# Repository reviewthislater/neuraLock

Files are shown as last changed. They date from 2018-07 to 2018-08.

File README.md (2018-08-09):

<div align="center">

# neuraLock



#### A proof of concept safe utilizing deep learning for facial, vocal, and word recognition.
#### Contains code and STLS to build your own nueraLock safe

 []()

</div>

## Hardware
[Raspberry Pi 3 Model B](https://www.amazon.com/gp/product/B01LPLPBS8/ref=oh_aui_detailpage_o00_s00?ie=UTF8&psc=1): $35.99

[Samsung Evo Micro SD](https://www.amazon.com/Samsung-MicroSDXC-Adapter-MB-ME64GA-AM/dp/B06XX29S9Q): $17.99

[Keyboard w/ trackpad](https://www.amazon.com/Rii-Wireless-Keyboard-Touchpad-Control/dp/B00I5SW8MC): $15.95

[Traxxas Servo](https://www.amazon.com/dp/B000XQ3G3E): $26.05

[ELP Mini USB Camera](https://www.amazon.com/gp/product/B01DRJXDEA): $29.99

[Lavalier Mini USB Microphone](https://www.amazon.com/gp/product/B074BLM973): $14.99

[5000 mAh External Battery](https://www.amazon.com/gp/product/B00MWU1GGI): $11.99

[Assorted LEDS](https://www.amazon.com/Lights-Emitting-Assortment-Arduino-300-Pack/dp/B00UWBJM0Q): $9.99

[Tactile Switches](https://www.amazon.com/Uxcell-a15111200ux1613-Momentary-Tactile-Terminal/dp/B019DCWTSQ): $7.46

3d printer and filament: $??.??

#### Total Cost: 170.40 + ??.??

All of these parts except for the raspberry pi 3 can be exchanged with similar parts, the provided links provide either the exact or similar hardware I used.

## Setup & Install
### Clone the repository
```bash
cd ~
git clone https://github.com/alexanderepstein/neuraLock
```
### Enter the repository
```bash
cd neuraLock
```
### Run environment build script
```
./env.sh
```
The script will ask for sudo privileges.
### Build training dataset
For both image and audio data the folder structure should look like
```bash
├── AudioData
│   ├── Subject1
│   │   ├── file1.wav
│   │   ├── file2.wav
│   │   ├── file3.wav
│   ├── Subject2
│   │   ├── file1.wav
│   │   ├── file2.wav
│   ├── Subject3
│   │   ├── file1.wav
│   │   ├── file2.wav
│   │   ├── file3.wav
```

### Gathering Face Training Data
I used about 8 subjects from the [Yale Faces Extended B](http://vision.ucsd.edu/~leekc/ExtYaleDatabase/ExtYaleB.html) training set, the larger the number of subjects used the more robust the classifier will be. Also make sure to include pictures of any users you would like to be able to be validated for entering the safe, for better results take pictures with the same camera that will be used for prediction.

### Gathering Audio Training Data
I used about 5 subjects from the [VoxForge dataset](http://www.repository.voxforge1.org/downloads/SpeechCorpus/Trunk/Audio/Original/), it is useful to utilize training data with the same sampling rate as your microphone. It is also useful to get training data from the same individual recorded at different times, something like [Angus-CJG](http://www.repository.voxforge1.org/downloads/SpeechCorpus/Trunk/Audio/Original/48kHz_16bit/Angus-20080320-cjg.tgz)
and [Angus-NDD](http://www.repository.voxforge1.org/downloads/SpeechCorpus/Trunk/Audio/Original/48kHz_16bit/Angus-20080320-ndd.tgz) the wav files from both of these archives would go under one folder named Angus in the AudioData root directory. It is helpful to also record empty noise with about 10-20 samples 5 seconds each. This will classify noise with no speaker as this dummy subject. Finally make sure to record audio of any user you would like to be able to be validated for entering the safe, for better results record the audio with the same microphone that will be used for prediction.

### Wiring The Hardware
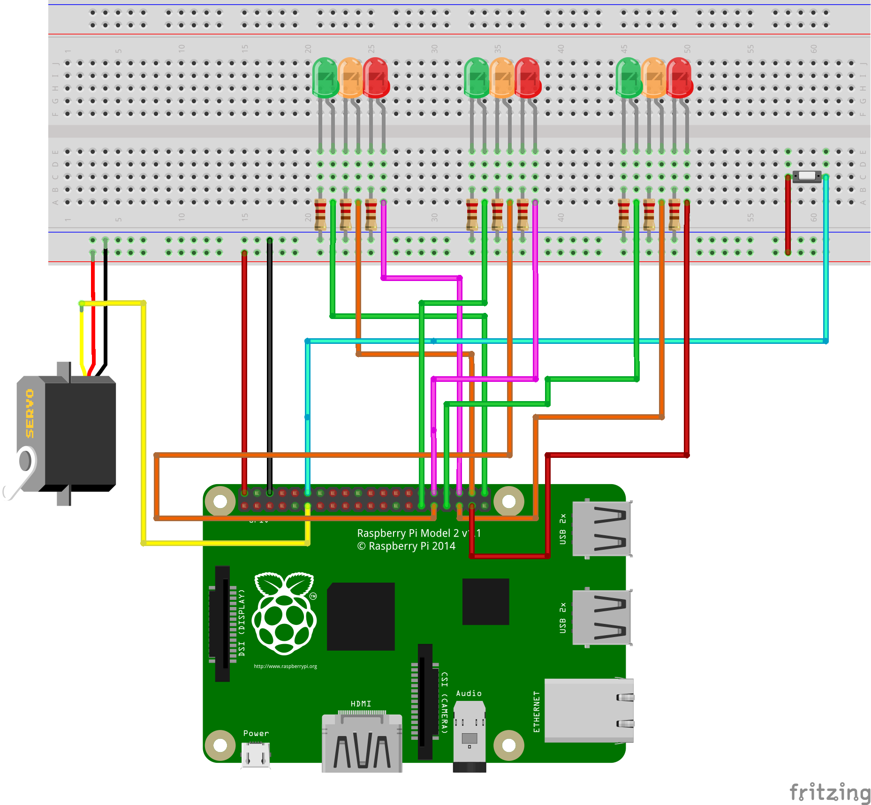
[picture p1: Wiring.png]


The pin layout will be treated as BCM, to see what that looks like visit [here](https://gpiozero.readthedocs.io/en/stable/recipes.html#pin-numbering)

| Component | GPIO |
|:---:|---|
| Servo |  17  |
| Push Button |  18  |
| Safe Green LED |  21  |
| Safe Orange LED  |  20  |
| Safe Red LED |  16  |
| Face Green LED |  13  |
| Face Orange LED  |  19  |
| Face Red LED |  26  |
| Voice Green LED  | 5  |
| Voice Orange LED | 6  |
| Voice Red LED |  12  |

### Executing the program

#### Command line arguments
```bash
-ad AUDIO_DATASET, --audio_dataset AUDIO_DATASET
                      path to audio training data
 -fd FACE_DATASET, --face_dataset FACE_DATASET
                       path to face training data
 -vm VOICE_MODEL, --voice_model VOICE_MODEL
                       path to serialized voice model
 -fm FACE_MODEL, --face_model FACE_MODEL
                       path to serialized face model
 -lv, --load_voice_model
                       boolean for loading voice model
 -lf, --load_face_model
                       boolean for loading face model
 -u UNLOCK_PHRASE, --unlock_phrase UNLOCK_PHRASE
                       unlock phrase
 -am {both,face,voice}, --authentication_model {both,face,voice}
                       choose the authentication model
 -vu VALID_USERS [VALID_USERS ...], --valid_users VALID_USERS [VALID_USERS ...]
                       users the safe should open for
```
A valid execution of the program might look like
```bash
./controller.py -ad "AudioData" -fd "ImageData" -vm "voiceModel.bin" -fm "imageEncodings.bin" -lv -am both -vu Alex
# Execute the program, audio data is located in AudioData, image data is contained in "ImageData", the voice model should be read to/written from "voiceModel.bin", the face encodings should be read to/written from "imageEncodings.bin", load the voice model, authenticate using both voice and face, set Alex as a valid user
```

### Current State
The STLS are not perfectly designed for the hardware, not enough testing was able to be done before confirm the design. However you can (force) the design to work by drilling and hot glue. You can use the STL's as a reference or starting point for what the safe will look like. Hopefully we will have time in the future to perfect the design.

### Issues
For any issues please open a new issue in the issue tracker [here](https://github.com/alexanderepstein/neuraLock/issues/new)

## License

MIT License

Copyright (c) 2018 Alex Epstein

Permission is hereby granted, free of charge, to any person obtaining a copy of this software and associated documentation files (the "Software"), to deal in the Software without restriction, including without limitation the rights to use, copy, modify, merge, publish, distribute, sublicense, and/or sell copies of the Software, and to permit persons to whom the Software is furnished to do so, subject to the following conditions:

The above copyright notice and this permission notice shall be included in all copies or substantial portions of the Software.

THE SOFTWARE IS PROVIDED "AS IS", WITHOUT WARRANTY OF ANY KIND, EXPRESS OR IMPLIED, INCLUDING BUT NOT LIMITED TO THE WARRANTIES OF MERCHANTABILITY, FITNESS FOR A PARTICULAR PURPOSE AND NONINFRINGEMENT. IN NO EVENT SHALL THE AUTHORS OR COPYRIGHT HOLDERS BE LIABLE FOR ANY CLAIM, DAMAGES OR OTHER LIABILITY, WHETHER IN AN ACTION OF CONTRACT, TORT OR OTHERWISE, ARISING FROM, OUT OF OR IN CONNECTION WITH THE SOFTWARE OR THE USE OR OTHER DEALINGS IN THE SOFTWARE.

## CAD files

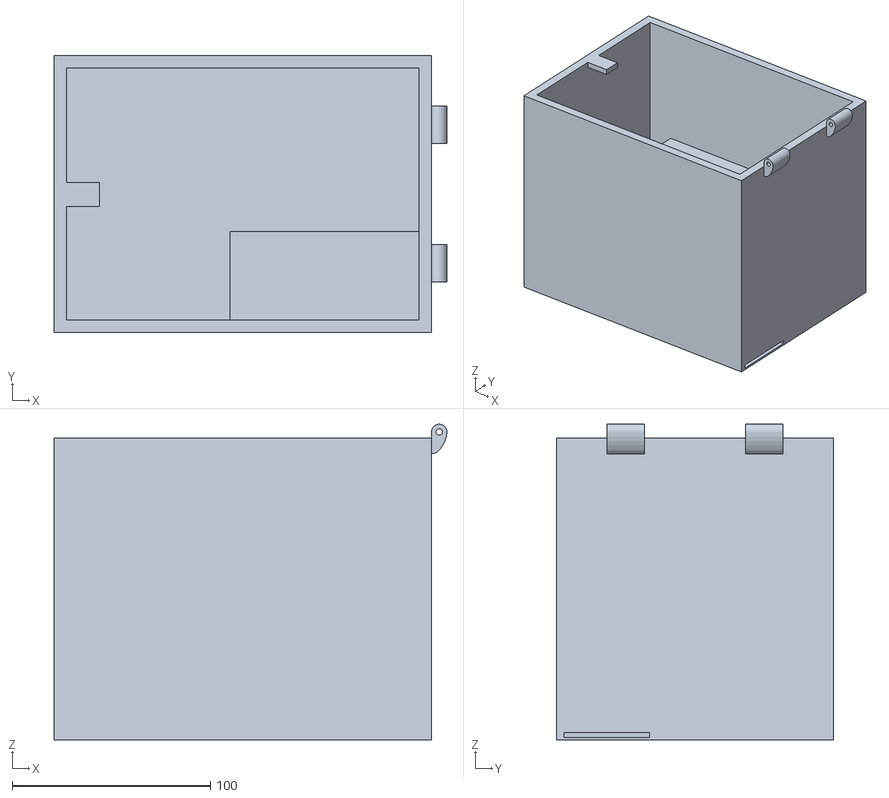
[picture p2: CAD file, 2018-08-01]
STL/container.STL
198.4 x 139.7 x 159.3

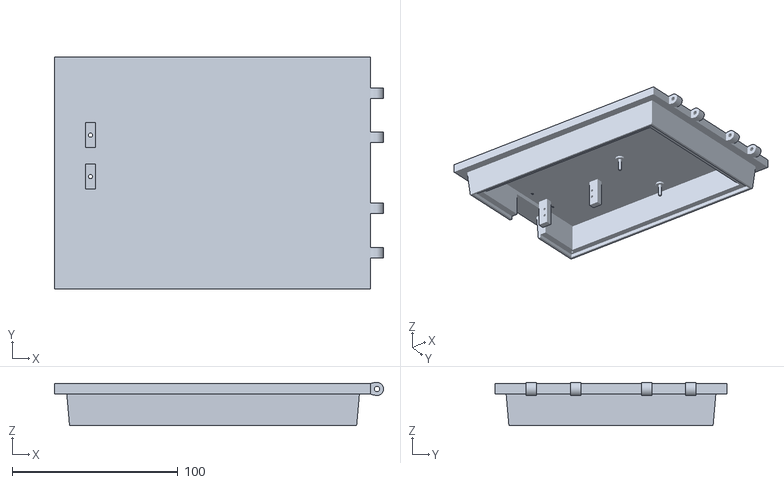
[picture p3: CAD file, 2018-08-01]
STL/door.STL
198.4 x 139.7 x 26.0

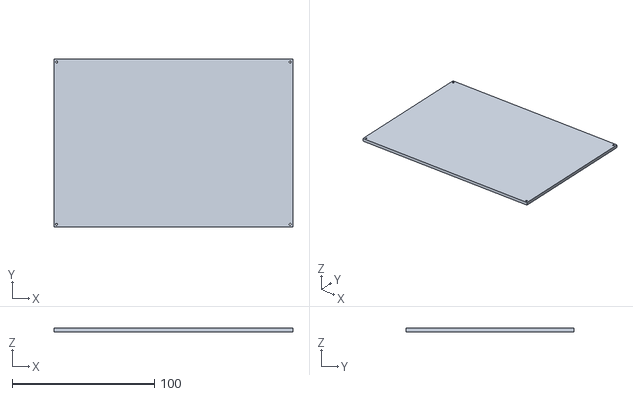
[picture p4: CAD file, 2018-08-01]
STL/doorCover.STL
168.0 x 118.0 x 2.50

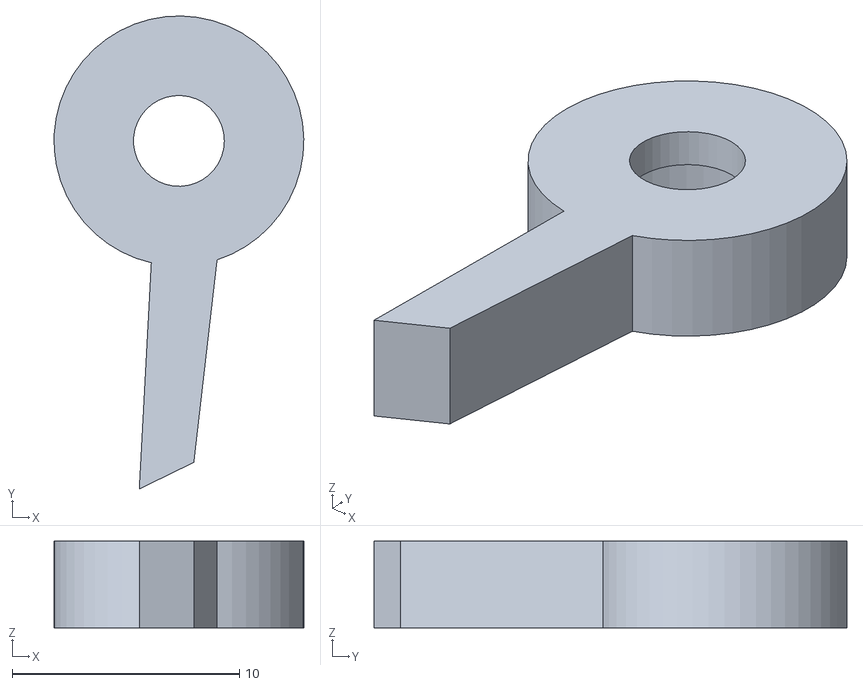
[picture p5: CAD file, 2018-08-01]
STL/servoAttachment.STL
11.0 x 20.8 x 3.81

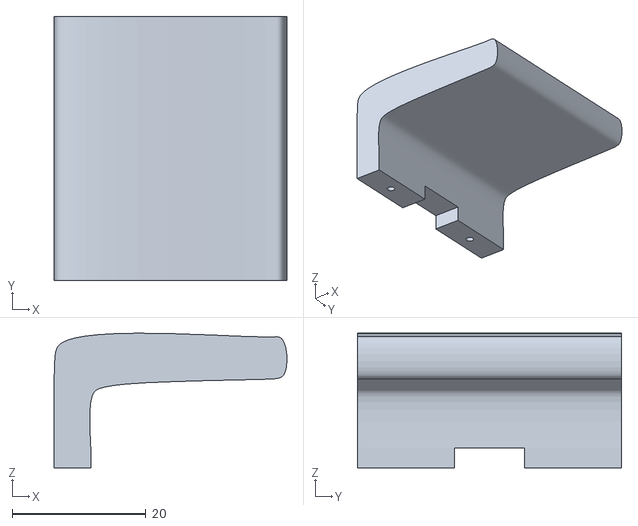
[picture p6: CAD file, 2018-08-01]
STL/doorHandle.STL
34.9 x 39.5 x 20.1

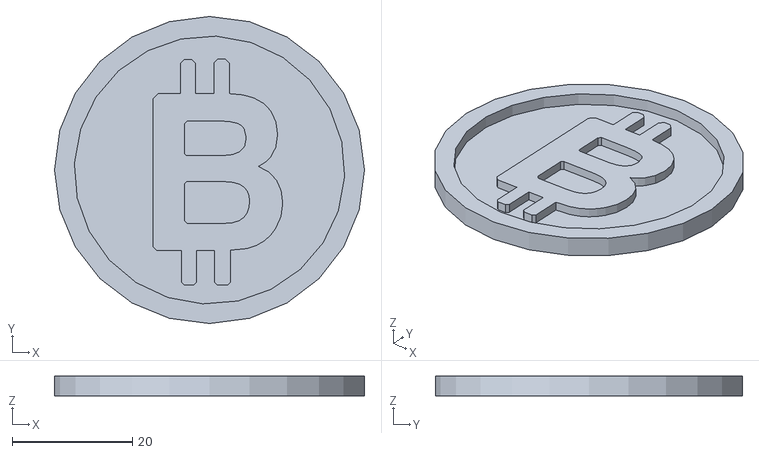
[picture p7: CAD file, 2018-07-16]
STL/bitcoin.stl
51.5 x 51.0 x 3.30

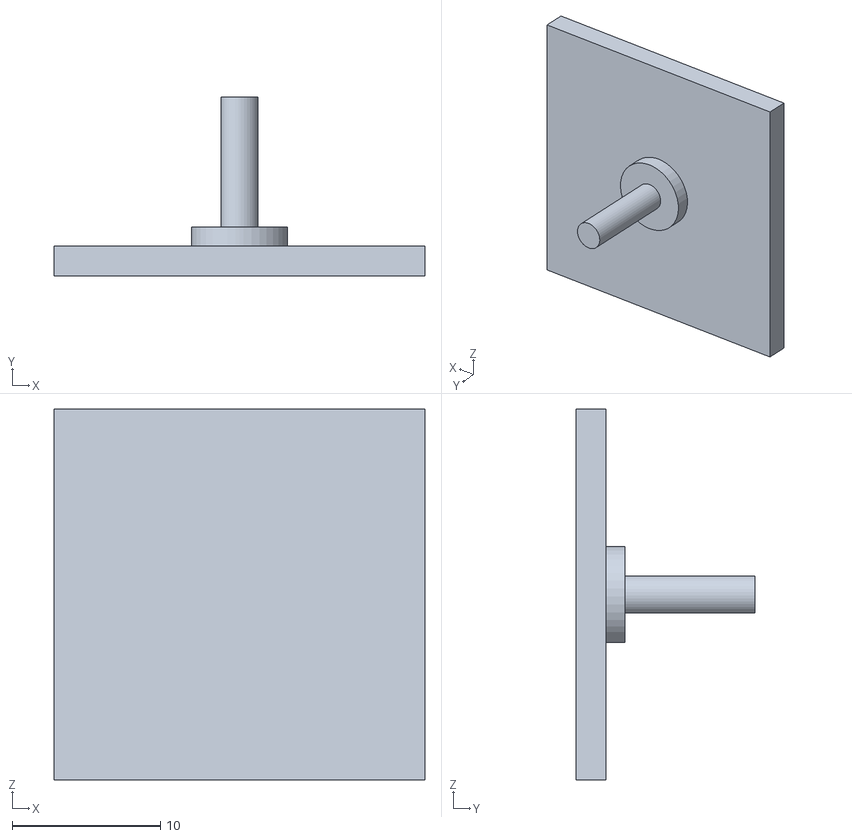
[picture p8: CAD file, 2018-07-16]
STL/testTab.STL
25.0 x 12.0 x 25.0

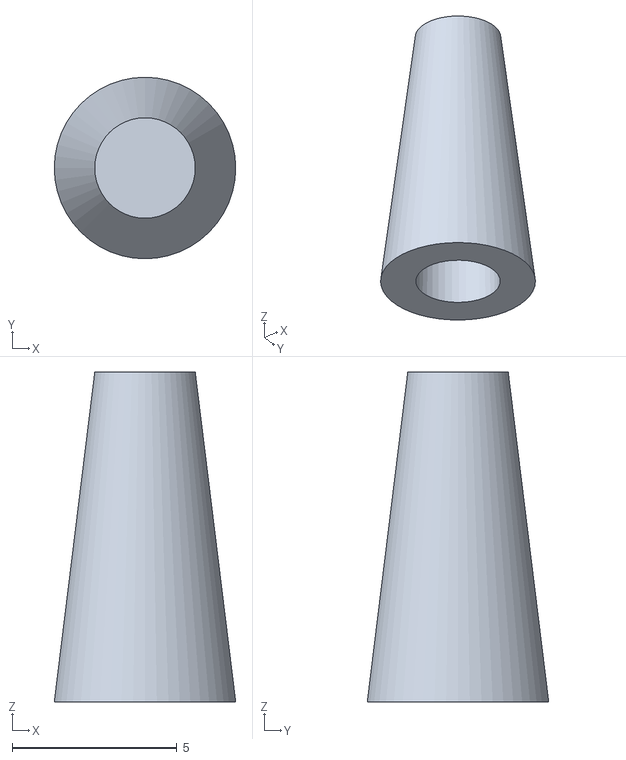
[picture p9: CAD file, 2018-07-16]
STL/capForTab.STL
5.50 x 5.50 x 10.0

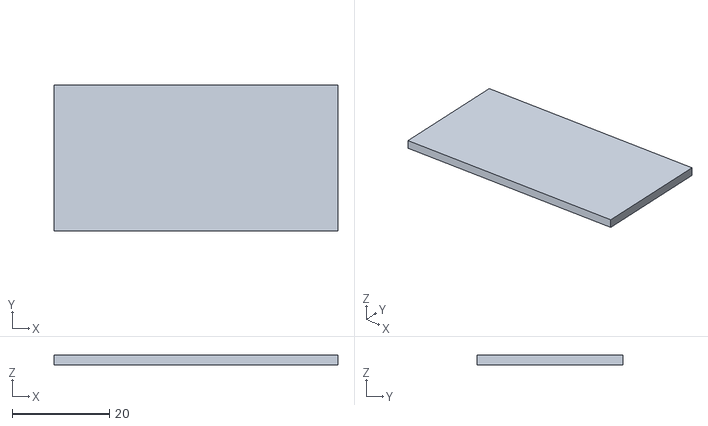
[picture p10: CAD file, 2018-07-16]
STL/batteryDoor.STL
58.4 x 30.0 x 2.00

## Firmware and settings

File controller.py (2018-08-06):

#!/usr/bin/env python3
from Recognizers.VoiceRecognizer import VoiceRecognizer
from Recognizers.FaceRecognizer import FaceRecognizer
from Recognizers.utilities import utilities
from scipy.io.wavfile import read
from time import sleep
import numpy as np
import argparse
import torch.optim as optim
from gpiozero import Servo, Button, LED

servo = Servo(17)
safeGreenStatus = LED(21)
safeOrangeStatus = LED(20)
safeRedStatus = LED(16, initial_value=True)
voiceGreenStatus = LED(5)
voiceOrangeStatus = LED(6)
voiceRedStatus = LED(12, initial_value=True)
faceGreenStatus = LED(13)
faceOrangeStatus = LED(19)
faceRedStatus = LED(26, initial_value=True)
lockButton = Button(18)
servo.value = -1
sleep(2)
servo.value = None
sleep(2)

def setSafeStatus(status):
	if status == "red":
		safeOrangeStatus.off()
		safeGreenStatus.off()
		safeRedStatus.on()
	elif status == "green":
		safeRedStatus.off()
		safeOrangeStatus.off()
		safeGreenStatus.on()
	elif status == "orange":
		safeRedStatus.off()
		safeGreenStatus.off()
		safeOrangeStatus.on()

def setVoiceStatus(status):
	if status == "red":
		voiceOrangeStatus.off()
		voiceGreenStatus.off()
		voiceRedStatus.on()
	elif status == "green":
		voiceRedStatus.off()
		voiceOrangeStatus.off()
		voiceGreenStatus.on()
	elif status == "orange":
		voiceRedStatus.off()
		voiceGreenStatus.off()
		voiceOrangeStatus.on()
	elif status == "off":
		voiceRedStatus.off()
		voiceGreenStatus.off()
		voiceOrangeStatus.off()


def setFaceStatus(status):
	if status == "red":
		faceOrangeStatus.off()
		faceGreenStatus.off()
		faceRedStatus.on()
	elif status == "green":
		faceRedStatus.off()
		faceOrangeStatus.off()
		faceGreenStatus.on()
	elif status == "orange":
		faceRedStatus.off()
		faceGreenStatus.off()
		faceOrangeStatus.on()
	elif status == "off":
		faceRedStatus.off()
		faceGreenStatus.off()
		faceOrangeStatus.off()

def unlock(state):
	setSafeStatus("green")
	servo.value = 1
	sleep(2)
	servo.value=None
	state = "unlocked"
	print("State: ", state)
	return state

def lock(state):
	setSafeStatus("red")
	servo.value = -1
	sleep(2)
	servo.value = None
	state = "locked"
	print("State: ",state)
	return state


def driver():
	ap = argparse.ArgumentParser(
	prog="neuraLock",
	description="DIY safe utilizing facial and vocal recognition",
	epilog="By: Alex Epstein https://github.com/alexanderepstein\n&\nDave Wigley https://github.com/davidwigley")
	ap.add_argument("-ad", "--audio_dataset", help="path to audio training data", required=True)
	ap.add_argument("-fd", "--face_dataset",  help="path to face training data", required=True)
	ap.add_argument("-vm", "--voice_model", help="path to serialized voice model", required=True)
	ap.add_argument("-fm", "--face_model", help="path to serialized face model", required=True)
	ap.add_argument("-lv", "--load_voice_model", help="boolean for loading voice model", default=False, action="store_true")
	ap.add_argument("-lf", "--load_face_model", help="boolean for loading face model", default=False, action="store_true")
	ap.add_argument("-u", "--unlock_phrase", help="unlock phrase", default="")
	ap.add_argument("-am", "--authentication_model", choices=["both", "face", "voice"], default="both", help="choose the authentication model")
	ap.add_argument('-vu', '--valid_users', nargs='+', help="users the safe should open for", required=True)
	args = ap.parse_args()

	validUsers = args.valid_users
	state = "locked"

	if args.authentication_model == "both" or args.authentication_model == "face":
		fr = FaceRecognizer(validUsers ,detectionMethod="hog", encodings=args.face_model, imageDirectory=args.face_dataset)
		if args.load_face_model: fr.loadEncodings()
		else: fr.encodeImages()
		vs, fps = fr.setup()

	if args.authentication_model == "both" or args.authentication_model == "voice":
		_,_, trainNames = utilities.getFilePaths(args.audio_dataset)
		vr = VoiceRecognizer(len(trainNames), validUsers, unlockPhrase=args.unlock_phrase,
							savedModelPath=args.voice_model, audioDirectory=args.audio_dataset, names=trainNames)
		vr.optimizer = optim.Adam(vr.parameters(), lr=0.001)
		if args.load_voice_model: vr.loadModel()
		else:
			trainPaths, trainLabels, trainNames = utilities.getFilePaths(directory=args.audio_dataset)
			trainData = [read(audioFile) for audioFile in trainPaths] # Read in the audioData
			trainRates = np.array([audio[0] for audio in trainData]) # Grab the sampling rate
			trainSignals = np.array([audio[1] for audio in trainData]) # Grab the signals themselves
			trainLoader = vr.preprocessAudio(trainSignals, trainRates, loader=True, targets=trainLabels)
			vr.trainNetwork(trainLoader, epochs=300, debug=True)

	if args.authentication_model == "both":
		while True:
			bothAuthenticated = False
			setSafeStatus("orange")
			while not bothAuthenticated:
				setFaceStatus("orange")
				recognizedFaces = fr.run(vs, fps, debug=False)
				setFaceStatus("green")
				setVoiceStatus("orange")
				recognizedVoice = [vr.run()]
				if recognizedVoice != "Unknown":  setVoiceStatus("green")
				else:
					setVoiceStatus("red")
					continue
				userSet = set(recognizedFaces) & set(recognizedVoice) & set(validUsers) # make sure we are returning the same valid user
				if len(userSet) == 1:
					bothAuthenticated = True
					state = unlock(state)

			while state == "unlocked":
				if lockButton.is_pressed:
					state = lock(state)
					setVoiceStatus("red")
					setFaceStatus("red")
					vs, fps = fr.setup()
					sleep(5)

	elif args.authentication_model == "voice":
		setFaceStatus("off")
		while True:
			voiceAuthenticated = False
			setSafeStatus("orange")
			while not voiceAuthenticated:
				setVoiceStatus("orange")
				recognizedVoice = [vr.run()]
				userSet = set(recognizedVoice) & set(validUsers)

				if len(userSet) == 1:
					setVoiceStatus("green")
					voiceAuthenticated = True
					state = unlock(state)

			while state == "unlocked":
				if lockButton.is_pressed:
					state = lock(state)
					setVoiceStatus("red")

	elif args.authentication_model == "face":
		setVoiceStatus("off")
		while True:
			faceAuthenticated=False
			setSafeStatus("orange")
			while not faceAuthenticated:
				setFaceStatus("orange")
				recognizedFaces = fr.run(vs, fps, debug=False)
				setFaceStatus("green")
				if len(recognizedFaces) == 1:
					faceAuthenticated = True
					state = unlock(state)

			while state == "unlocked":
				if lockButton.is_pressed:
					state = lock(state)
					setFaceStatus("red")
					vs, fps = fr.setup()
					sleep(5)

if __name__ == "__main__": driver()

#./controller.py -ad "AudioData" -fd "ImageData" -vm "voiceModel.bin" -fm "imageEncodings.bin" -lv -am both -vu Alex Dave

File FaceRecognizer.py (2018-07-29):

#!/usr/bin/env python3
# import the necessary packages
from imutils.video import VideoStream, FPS
import face_recognition as fr
import imutils
import pickle
import time
import cv2
import os
import sys
import warnings

class FaceRecognizer(object):

	def __init__(self, validUsers, detectionMethod="hog", encodings="imageEncodings.bin", detector=cv2.CascadeClassifier(sys.path[0] + "/lbpcascade_frontalface.xml")):
		self.detectionMethod = detectionMethod # Default to hog which is 128d feature extraction and linear svm
		self.encodings = encodings #pickled encodings, should only need to encode once
		self.detector = detector # lbp is faster than haar cascade
		assert type(validUsers) == type([])
		self.validUsers = validUsers # list of validUsers

	def getImageData(self, rootDirectory="ImageData"):
		images = [] # images with exactly one face
		imagePaths = [] # paths to all the images
		validPaths = [] # paths to images with only 1 face detected
		imageDirectory = sys.path[0] + "/" + rootDirectory # looks for the root directory relative to where the script was run because python needs absolute paths (add to sys.path for relative paths)
		# Grab image paths
		for label in os.listdir(imageDirectory): # for each folder in the image directory
		    for image in os.listdir(imageDirectory + "/" + label): # for each file in each folder
		       imagePaths.append(imageDirectory + "/" + label + "/" + image) #add to the image pathh
		# Determine valid images (exactly one face needs to be detected to be a valid image)
		for imagePath in imagePaths:
		    original = cv2.imread(imagePath)
		    image = original #if opencv else original
		    faces = detector.detectMultiScale(image, scaleFactor=1.1, minNeighbors=5, minSize=(30, 30)) # change scale factor here if faces aren't being detected, it relates to how far the person is from the camera
		    if len(faces) != 1: warnings.warn("Not using an image from the train data set because exactly one face was not detected")
		    else: validPaths.append(imagePath)
		return validPaths


	def encodeImages(self):
	    	print("[INFO] quantifying faces...")
	    	imagePaths, labels = getImageData() #  grab the paths to the input images in our dataset
	    	knownEncodings = []
	    	knownNames = []

	    	for (i, imagePath) in enumerate(imagePaths): # loop over the image paths
	    		print("[INFO] processing image {}/{}".format(i + 1,len(imagePaths)))
	    		name = imagePath.split(os.path.sep)[-2] # extract the person name from the image path
	    		image = cv2.imread(imagePath) # load image
	    		rgb = cv2.cvtColor(image, cv2.COLOR_BGR2RGB) # convert to rgb
	    		faces = fr.face_locations(rgb, model=detectionMethod) # detect box around face
	    		encodings = fr.face_encodings(rgb, faces) # compute the facial embedding for the face
	    		for encoding in encodings: # loop over the encodings
	    			knownEncodings.append(encoding) # add each encoding to knownEncodings
	    			knownNames.append(name) # add each name to knownNames
	    	print("[INFO] serializing encodings...")
	    	data = {"encodings": knownEncodings, "names": knownNames}
	    	f = open(self.encodings, "wb")
	    	f.write(pickle.dumps(data)) # dump the facial encodings + names to disk
	    	f.close()

	def setup(self):
		print("[INFO] loading encodings + face detector...")
		data = pickle.loads(open(self.encodings, "rb").read()) # load the known faces and embeddings along with lbp for face detection
		print("[INFO] starting video stream...")
		vs = VideoStream(src=0).start() # initialize the video stream and allow the camera sensor to warm up
		time.sleep(2.0)
	    	# start the FPS counter
		fps = FPS().start()
		return data, vs, fps

	def run(self, data, vs, fps, debug=True):
		continousPredictions = 0
		lastPrediction = ""
	    	# loop over frames from the video file stream
		while continousPredictions <=3:
			frame = vs.read() # grab the frame from the threaded video stream
			frame = imutils.resize(frame, width=500) # resize to 500px (to speedup processing)
			gray = cv2.cvtColor(frame, cv2.COLOR_BGR2GRAY) # convert the input frame from (1) BGR to grayscale (for face detection)
			rgb = cv2.cvtColor(frame, cv2.COLOR_BGR2RGB) # (2) from BGR to RGB (for face recognition)

			rects = self.detector.detectMultiScale(gray, scaleFactor=1.1, minNeighbors=5, minSize=(30, 30)) 	# detect faces in the grayscale frame
	    		# OpenCV returns bounding box coordinates in (x, y, w, h) order
	    		# but we need them in (top, right, bottom, left) order, so we
	    		# need to do a bit of reordering
			boxes = [(y, x + w, y + h, x) for (x, y, w, h) in rects]
			encodings = fr.face_encodings(rgb, boxes) # compute the facial embeddings for each face bounding box
			names = []
	    		# loop over the facial embeddings
			for encoding in encodings:
				matches = fr.compare_faces(data["encodings"], encoding) # attempt to match each face in the input image to our known encodings
				name = "Unknown"

	    			# check to see if we have found a match
				if True in matches:
	    				# find the indexes of all matched faces then initialize a
	    				# dictionary to count the total number of times each face
	    				# was matched
					matchedIdxs = [i for (i, b) in enumerate(matches) if b]
					counts = {}

	    				# loop over the matched indexes and maintain a count for
	    				# each recognized face face
					for i in matchedIdxs:
						name = data["names"][i]
						counts[name] = counts.get(name, 0) + 1

	    				# determine the recognized face with the largest number
	    				# of votes (note: in the event of an unlikely tie Python
	    				# will select first entry in the dictionary)
					name = max(counts, key=counts.get)
	    			# update the list of names
				names.append(name)
	    			# loop over the recognized faces
			if any(face in self.validUsers for face in names): continousPredictions += 1
			else: continousPredictions = 0

			if debug:
				for ((top, right, bottom, left), name) in zip(boxes, names):
					# draw the predicted face name on the image
					cv2.rectangle(frame, (left, top), (right, bottom), (0, 255, 0), 2)
					y = top - 15 if top - 15 > 15 else top + 15
					cv2.putText(frame, name, (left, y), cv2.FONT_HERSHEY_SIMPLEX, 0.75, (0, 255, 0), 2)
					# display the image to our screen
					cv2.imshow("Frame", frame)
					key = cv2.waitKey(1) & 0xFF
					if key == ord("q"): break # if the `q` key was pressed, break from the loop
					fps.update() # update the FPS counter
		if debug:
			 # stop the timer and display FPS information
			fps.stop()
			print("[INFO] elasped time: {:.2f}".format(fps.elapsed()))
			print("[INFO] approx. FPS: {:.2f}".format(fps.fps()))
			# do a bit of cleanup
			cv2.destroyAllWindows()
			vs.stop()

		return set.union(set(names), set(self.validUsers))# detected users


if __name__ == "__main__":
	FR = FaceRecognizer(["Alex"])
	#FR.encodeImages()
	data, vs, fps= FR.setup()
	FR.run(data, vs, fps, debug=True)

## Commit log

2018-07-16 Uploading STL files
    [Bit_coin.stl, Capfortab_v3.STL, battery_door.STL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]
2018-07-16 Name Change of STL files
    deleted part of the name of each file that had multiple versions, i.e.
    "servo_attachment_v6"
    [Capfortab.STL, container.STL, servo_attachment.STL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]
2018-07-29 fixed userset logic and spacing
    [controller.py]
2018-07-29 fixed returnset logic and indentation
    [FaceRecognizer.py]
2018-08-01 Uploading .Stl files
    [Capfortab_v3.STL, Door_cover.STL, Door_handle.STL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]
2018-08-02 Renaming STLS
    [batteryDoor.STL, bitcoin.stl, capForTab.STL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]
2018-08-05 Adding wiring diagram
